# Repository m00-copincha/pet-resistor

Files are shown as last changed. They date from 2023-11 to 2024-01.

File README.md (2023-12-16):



# What is PET-Resistor?

PET-Resistor is a PET bottle 3D printing filament extruder, akin to [TheRecreator3D](http://recreator3d.com/), [Petamentor](https://petamentor2.com), and [PETalot](https://github.com/function3d/petalot), [FixStruder](https://www.fixstruder.eu/product/fixbot/). It combines the best features of these projects, emphasizing purpose and simplicity. Here are the key characteristics of PET-Resistor:

* **Self-replication:** the PET-Resistor filament extruder has self-replication capabilities like RepRap machines (https://reprap.org/wiki/RepRap), allowing it to contribute to its own production cycle.

* **Flat components:** we have adopted a pragmatic approach using flat components. These parts are designed using open source CAD software (such as Solvespace, OpenSCAD, Inkscape). These parts can be manufactured by laser, milling machine or 3D printing, which ensures their accessibility.

* **Inclusive design:** We intentionally minimize the manufacturing skills required so that more people can actively participate. We use the Openstructure modular system (https://www.openstructures.net/), which provides a common framework for adapting and creating components, encouraging collaboration and innovation.

Feel free to reach me out if you have any questions or want to get involved! 🌱🌟

# Contents

- [Getting Started](#getting-started)
- [Documentation](#documentation)
    - [Building the machine](#building-the-machine)
        - [Prerequisites](#prerequisites)
        - [Components](#components)
        - [The building flow](#the-building-flow)
    - [Using the machine](#using-the-machine) 
        - [Preparing the bottles](#preparing-the-bottles)
        - [Cutting the strips](#cutting-the-strips)
        - [Extruding](#extruding)
    - [3D printing with PET](#3d-printing-with-pet)

# Getting Started

For this project, you need the following programs:

* A 2D vector drawing software. You can use any one that allows you to export in SVG format. I am using:
    * SolveSpace, which allows you to make drawings with parametric constraints.
    * Inkscape, which allows you to draw vector graphics in a simple way.
* A 3D modeling software. You can use OpenSCAD, which allows you to import SVG files and apply an extrusion operation to give them thickness.

Another option is to create the drawing and the extrusion directly in SolveSpace, without using another program.

# Documentation

## Building the machine

### Prerequisites

### Components

- A bottle cutter built by:
    - 1 Threaded rod M8
    - 2 screws M8
    - 2 wing nuts M8
    - 1 cutter blade 9mm

- A power supply system, built by:

    - Power supply 110V 12V 10Amp (or more)
    - On/Off Switch 
    - Powercord 2m 

- A system to generate temperature in a controlled way, built by:

    - 3D Printer Heater Cartridge Wire 12V 40W
    - 3d printer heating block
    - REX-C100 Temperature Controller
    - K Type Thermocouple Temperature Probe Sensor
    - Relay 12V 10Amp
    - Computer Fan 12V 50mm x 50mm

- A system to rotate the reel in a controlled way, built with:

    - [DC 12V RPM Gear Motor](https://www.amazon.com/gp/aw/d/B07K9KPWX6) - High Torque Electric Micro Speed Reduction Geared Motor Centric Output Shaft 37mm Diameter Gearbox
    - Potentiometer module for the speed control for 12V 10 Amp

- Mechanical parts and structures made with fabricated or standardized parts.
    - screws 
    - nut
    - washer
    - 8 brace

To better understand the project we can see it from the origin of its components, so we have:

Purchased Components: these are the components that are purchased in the market, such as screws, bearings, cables, etc.

Recycled components: these are the components obtained from other objects or machines in disuse. These components are used to reduce the cost and environmental impact of the RepRap project.

Fabricated Components: these are components that are created with a RepRap machine or other tools, such as 3D printers, milling machines, etc. These were designed following the Openstructures grid.

### The building flow

1. Preparing the cutter module
    1.1 Place the screws on the cutter base and attach the wing nuts.
    1.2 Place threaded rod on the cutter base.
    1.3 Attach the cutter base to the cutter holder by screwing it together.

2. Preparing the hotend module
    2.1. Drill the hotend with a 1.7 mm drill bit.
    2.2. Drill the back of the heater with a 5mm drill bit.
    2.3. Attach the hotend to the hotend holder.
    2.4. Attach the ribbon guide to the hotend holder.
    2.5. Place the thermocoupler on the heatblock
    2.6. Place the resistor on the heatblock
    2.7. Insert cables through the orifice of the hotend holder

3. Preparing the power supply module
    3.1. Screw the power supply unit to the brackets

4. Prepare the ventilation module 
    4.1. Screw the fan to the inlet and outlet ventilation brackets.

5. Prepare the winder module
    5.1. Screw motor to motor holder.
    5.2. screw coupling to motor
    5.3. Screw the spooler to the coupling
    5.4. Screw the spooler
    
6. Preparing the tensioning rod module
    6.1. Assemble the pulley
    6.2. Place the pulley inside the shaft
    6.3. Fit the inner guide nuts
    6.4. Place wing nuts as outer guides

7. Prepare control modules
    7.1. Place the power switch on its holder 
    7.2. Place Pid control on its holder
    7.3. Place the speed control on its support.

8. Prepare relay module
    8.1. Assemble the relay bracket
    8.2. Solder wires to the relay
    8.3. Attach relay to bracket
    
9. Screw the brackets with the power supply to the bars. 

10. Assemble the frame
    10.1. Join the aluminum bars and the 3 longest covers.

11. Fit the two side covers. Insert the power cable through the hole in one of these side covers.
    11.1. Connect the power cable to the switch. 11.2. 
    11.2. Connect the switch to the power supply.
    11.3. Connect the PID control to the power supply.
    11.4. Connect the fan to the power supply. 
    11.5. Connect the speed control to the power supply
    11.6. Connect the motor to the speed control
    11.7. Connect thermocouple to PID controller
    11.8. Connect the resistor to the PID control

12. Assemble front face
    12.1. Place control modules in the front frame. 12.2.
    12.2. place relay module on the front frame
    12.3. Place ventilation modules.

13. Assemble rear face

14. Assemble bottom face

## Using the machine?

### Preparing the bottles

* Check if you have a PET bottle, look for the triangle symbol with the number 1 on the inside.

* Remove the labels and wash the bottles well both inside and outside.

* Inflate the bottles by applying air pressure. 

* Remove creases using a hot air gun.

* Remove glue using WD-40 and a srub sponge or a scrub brush.

* Finally wash the bottle with detergent to remove any remaining grease.

### Cutting the strips

* Cut the bottles into strips using a cutter. 

* It is important that the tape is homogeneous to obtain a good quality filament. 

* The width of the strips should be between 8 and 9 mm. A bottle of water is about 11 or 12 meters. The wider the bottle is cut the shorter the resulting strip will be.

### Extruding

* Start the machine and set the appropriate temperature.

* Cut the end of the strip into a fine tip shape that can pass through the nozzle of the heating block.

* Insert the tip of the strip into the nozzle and pull it until the length of the resulting extruded filament is long enough to connect it to the spooling cable.

* Connect the tip of the resulting extruded filament to the winder cable.

## 3D printing with PET

1. Printer Compatibility:

    * Many common 3D printers are not designed for printing with PET.

    * Make sure your printer can operate above 250 degrees Celsius.

    * Verify that the Teflon tube is able to withstand temperatures up to 260 degrees Celsius.

    * Filament traction is better when using a direct extruder, as the Bowden system has higher friction.
    
    * Comprobar el barrel. Cambiar el barrel de la impresora si este no tiene un diametro suficientemente grande para el filamento PET.

    * Opt for a 0.6 mm or 0.8 mm nozzle.Pue ser que este no tenga al diametro suficiente 

2. Firmware setup: 

    * The firmware of the printers usually comes with a maximum temperature of 275 degrees Celsius, but it has set a maximum safety limit of 15% below this temperature. This prevents the printer from reaching the optimal working temperatures, which are between 250 and 265 degrees. 
    
    * If it is necessary, modify this limit and set it to 0.

3. Temperature control:

    * PET can crystallize and cause jams. Jams can be caused by:
    
        * High temperature.
        * Too slow printing speed.
        * Too fast Fan speed.

    * Start with a minimum temperature of 250 degrees Celsius and adjust as needed. Increase in 5 degree increments if extrusion is uneven or if filament slips.

3. Bubble control:

    * Bubbles are related to moisture. This is not absorbed directly by the filament, but is trapped in the void during manufacturing.

    * Dry the filament properly to avoid bubbles. You can use a filament dryer.

3. Printing parameters:

* Layer fan speed: Between 0-15%

* Printing temperature: Between 250°C and 260°C

* Hot bed temperature: Between 70°C and 85°C

* Printing speed: 30 mm/s

* Flow: 130%

<br>

**Cura**

* Select an standard PETG filament profile

* Vertical walls: 3
* Horizontal walls: 4 (If son bases cuadradas 5 o 6) 

* Distancia de linea relleno 15.0mm

* Flow Balance:
    * for  5mm ribbon thicknes: 160%
    * for 10mm ribbon thickness: 

* Retraction distence: 5.5 mm
* Retraction speed: 30 mps

* tree support:
    * angle: 45

* borde:
    * adherencia impresion:
        * ancho de borde: 6

* activar modo experimental usar capas adaptativas

<br>

**PrusaSlicer**

* Select an standard PETG filament profile

In Filament Settings:

* Filament tab

    * Filament
        * Extrusion multiplier: 1.3

    * Temperature

        * Nozzle
            * First layer: 260°C
            * Other layers: 260°C

        * Bed 
            * First layer: 70°C
            * Other layers: 70°C
        
* Cooling tab
    * Enable 
        * Keep fan always on: Unchecked
        * Enable autocooling: Unchecked

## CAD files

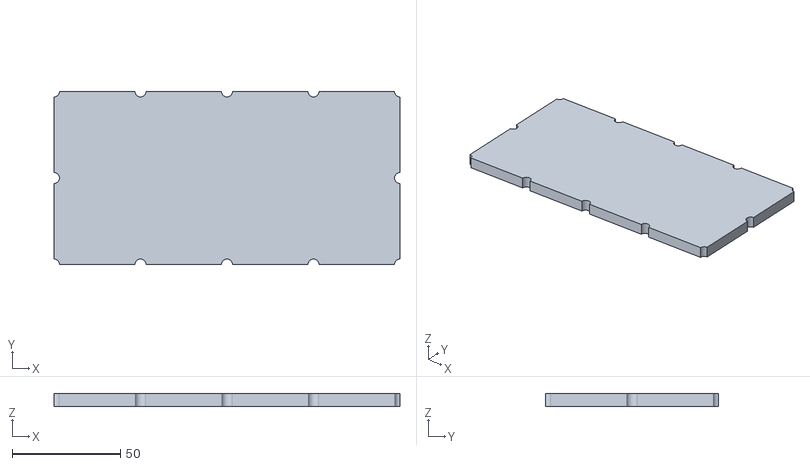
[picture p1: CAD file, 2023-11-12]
src/case/cover--back/cover--back--grid--logos.stl
160.0 x 80.0 x 6.00

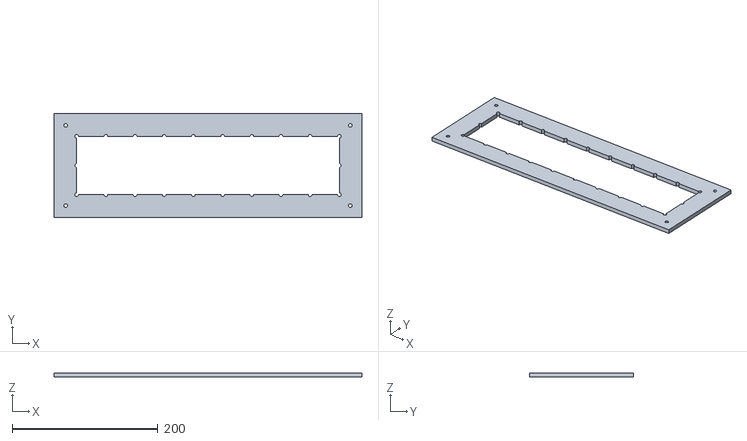
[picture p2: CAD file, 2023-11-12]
src/case/cover--bottom/cover--bottom--frame.stl
422.0 x 142.0 x 6.00

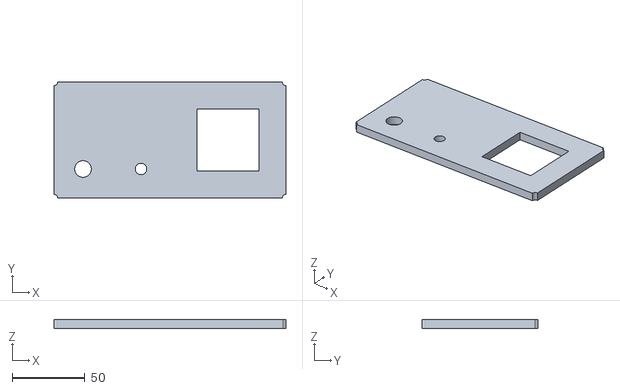
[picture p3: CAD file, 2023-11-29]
src/case/cover--front/cover--front--grid--control/cover--front--grid--control.stl
160.0 x 80.0 x 6.00

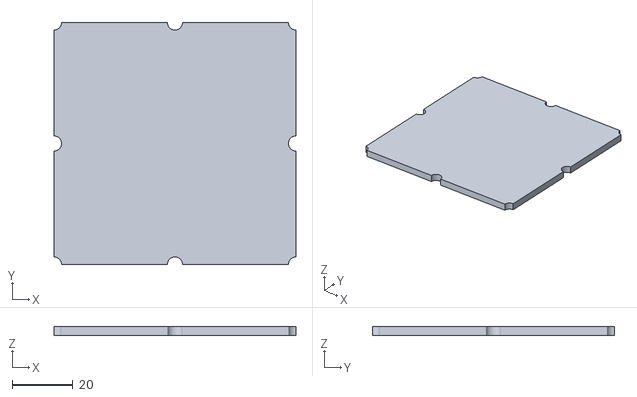
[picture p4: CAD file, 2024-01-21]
src/case/cover--grid--surface/cover--grid--surface--2x2.stl
80.0 x 80.0 x 3.00

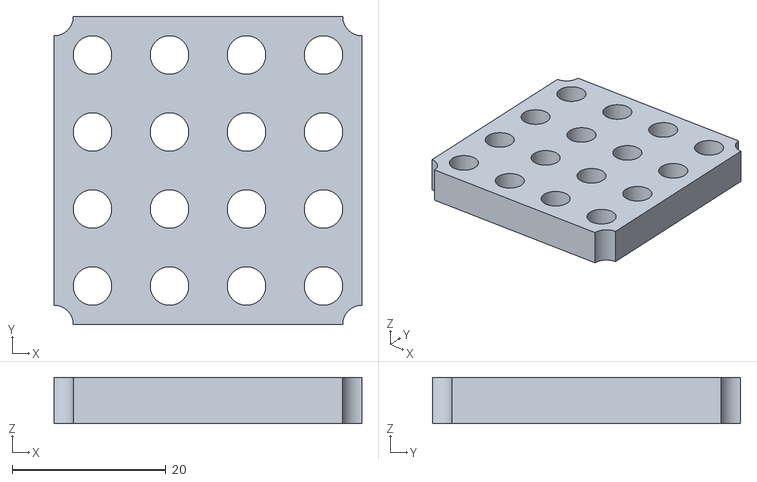
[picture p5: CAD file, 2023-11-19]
src/case/cover--grid--vent/cover--grid--vent--1x1.stl
40.0 x 40.0 x 6.00

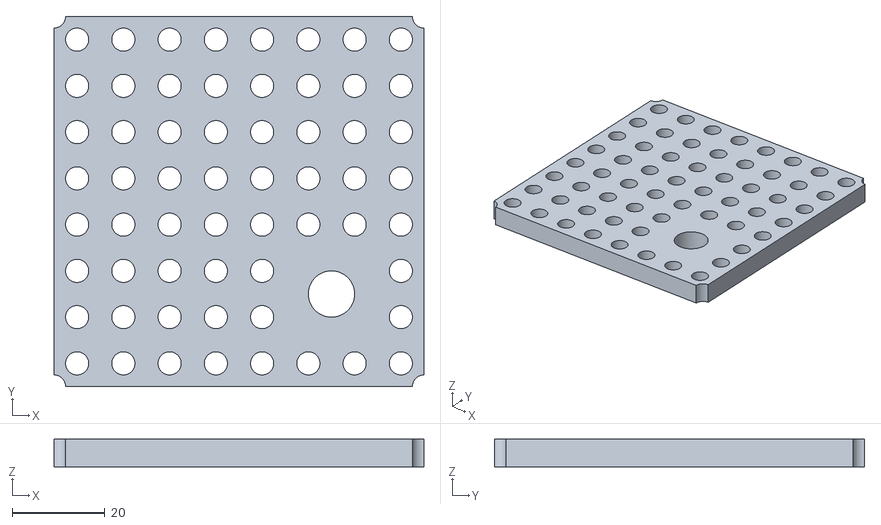
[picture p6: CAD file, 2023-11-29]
src/case/cover--left/cover--left--grid.stl
80.0 x 80.0 x 6.00

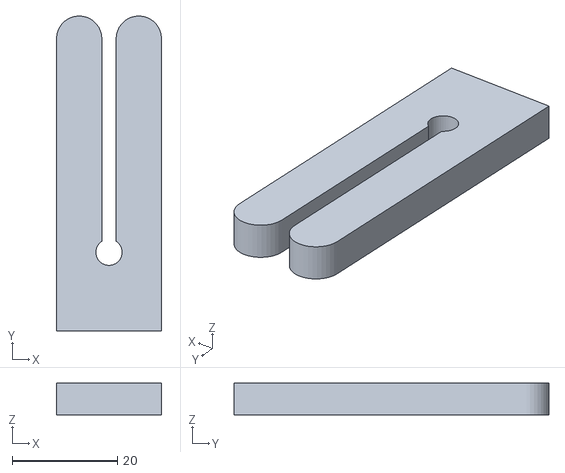
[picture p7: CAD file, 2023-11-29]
src/case/cover--top/cover--top--ribbon-holder.stl
20.0 x 60.0 x 6.00

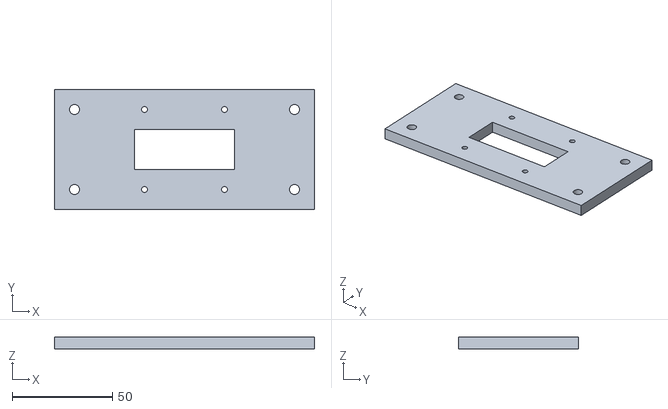
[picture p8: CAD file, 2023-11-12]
src/case/cover--top/fan-holder/case--fan-holder--ouput.stl
130.0 x 60.0 x 6.00

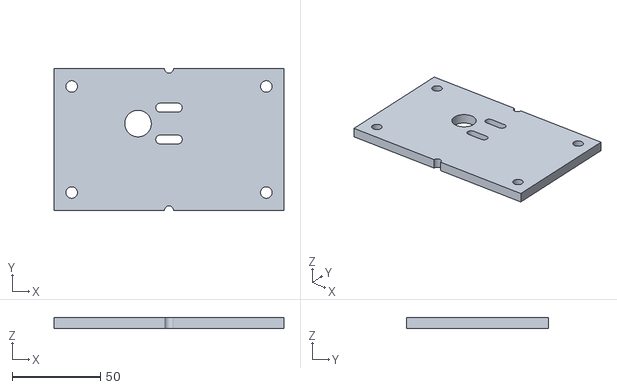
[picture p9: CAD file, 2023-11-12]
src/case/cover--top/hotend-holder/case--hotend-holder.stl
130.0 x 80.0 x 6.00

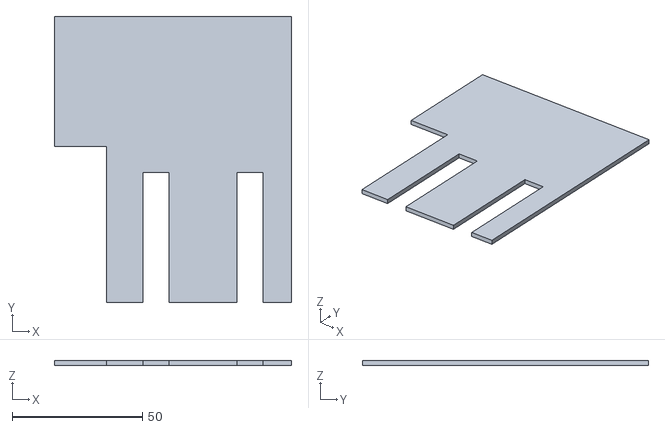
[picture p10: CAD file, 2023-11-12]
src/cutter--layout/cutter--layout.stl
91.0 x 110.0 x 2.00

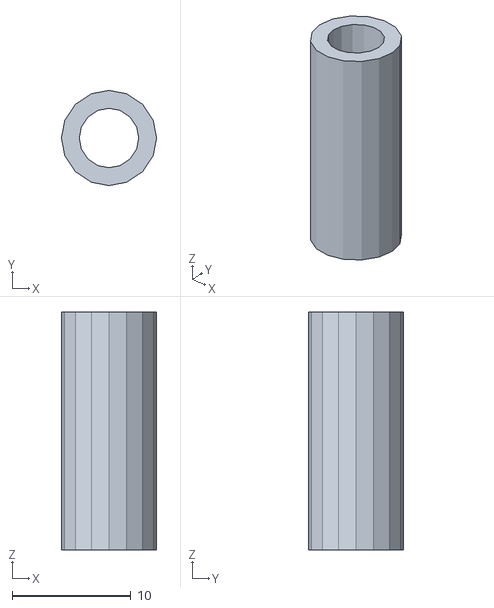
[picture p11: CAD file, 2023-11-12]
src/filament-hook--1.stl
8.00 x 8.00 x 20.0

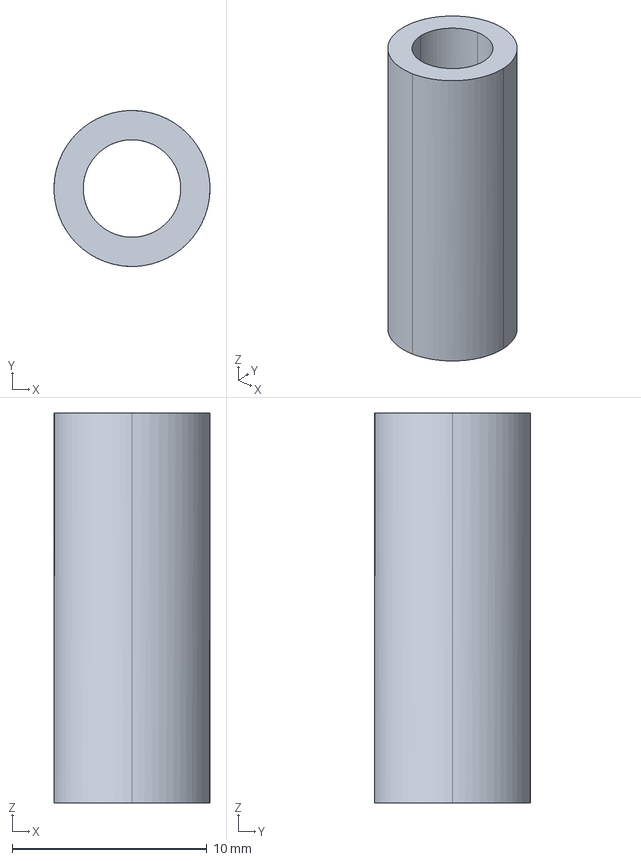
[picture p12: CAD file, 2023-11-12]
src/filament-hook/filament-hook--1.step
8.00 x 8.00 x 20.0 mm

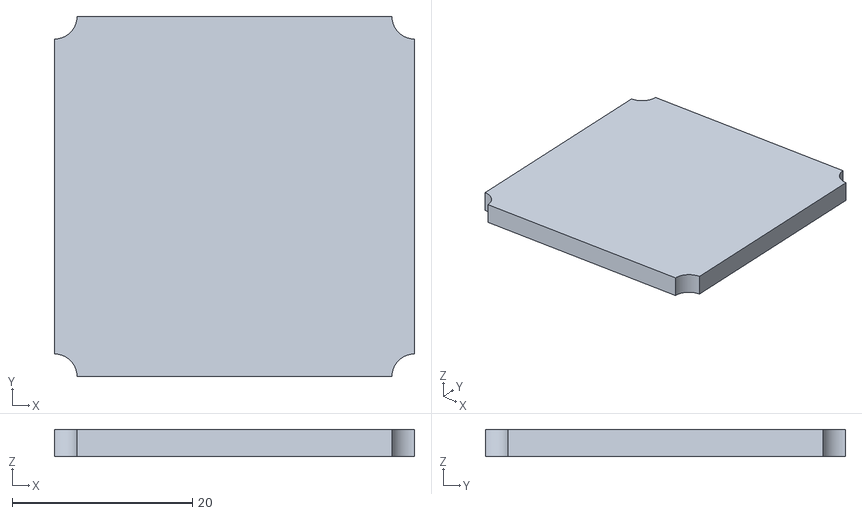
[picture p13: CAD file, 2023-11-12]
src/os-module/os-module--1x1.stl
40.0 x 40.0 x 3.00

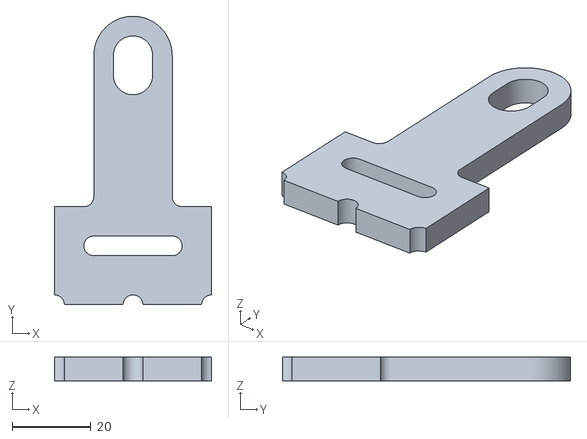
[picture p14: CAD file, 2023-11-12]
src/tensioning-rod/tensioning-rod--holder--m8.stl
40.0 x 73.5 x 6.00

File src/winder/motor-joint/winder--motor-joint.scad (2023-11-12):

//parameters

wall_thickness=3;
base_height=42;
coupling_thickness=8;
coupling_height=base_height-coupling_thickness;
svg_base="./winder--motor-joint--base.svg";
svg_hole_screw="./winder--motor-joint--hole--screw.svg";
svg_hole_coupling="./winder--motor-joint--hole--coupling.svg";


//operations

color("yellow")
translate([0,0,coupling_height-1]) 
linear_extrude(coupling_thickness+1)
import(svg_hole_coupling);

color("orange")
translate([0,0,coupling_height-wall_thickness])
linear_extrude(wall_thickness)
import(svg_hole_screw);

color("red")
linear_extrude(coupling_height)
import(svg_base);

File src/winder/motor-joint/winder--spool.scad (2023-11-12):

//modules

use <./winder--spool--front.scad>;
use <./winder--spool--base.scad>;


//parameters

wall_thickness=6;
spool_hight=42;


//operations

color("lightblue") 
translate ([0,0,spool_hight-wall_thickness])
winder_spool_front (h=wall_thickness);

color("blue") 
winder_spool_base (h_w=wall_thickness,h_s=spool_hight);

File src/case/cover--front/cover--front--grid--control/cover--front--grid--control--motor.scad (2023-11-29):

module cover_front_grid_control_motor (svg="./cover--front--grid--control--motor.svg",h=6) 
	{
	linear_extrude(h)
	import(svg);
	}

cover_front_grid_control_motor ();

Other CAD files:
src/case/cover--right/cover--right--grid.stl
src/winder/motor-joint/winder--motor-joint.stl
src/winder/spool/winder--spool--front.stl
src/case/cover--front/cover--front--grid--control/cover--front--grid--control--power.scad
src/case/cover--back/cover--back--frame.scad
src/case/cover--back/cover--back--grid--logos.scad
src/case/cover--back/cover--back--grid--vent.scad
src/case/cover--bottom/cover--bottom--frame.scad
src/case/cover--front/cover--front--frame.scad
src/case/cover--front/cover--front--grid--control/cover--front--grid--control--motor.stl
src/case/cover--front/cover--front--grid--control/cover--front--grid--control--pid.stl
src/case/cover--front/cover--front--grid--control/cover--front--grid--control--power.stl
src/case/cover--front/cover--front--grid--control/cover--front--grid--control--relay.scad
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

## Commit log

2023-11-12 adding parts and logo folders
    [bottle-cutter--body.stl, case--control--motor.scad, case--control--motor.stl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]
2023-11-12 moving parts in spool
    [bottle-cutter--body.stl, cutter--layout.scad, cutter--layout.stl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]
2023-11-14 adding text on readme.md
    [case--vent--1x1.scad]
2023-11-19 actualizando readme.md
    [case--vent--1x1.stl]
2023-11-29 updating readme
    [bottle-cutter--body.stl, case--control--motor.scad, case--control--motor.stl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]
2023-12-18 agregando video
    [bottle-cutter--body.stl, case--fan-holder--input.scad, case--fan-holder--input.stl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]
2023-12-18 actualizando src
    [bottle-cutter--body.stl, case--fan-holder--input.scad, case--fan-holder--input.stl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]
2024-01-21 update files
    [cover--front--grid--control--relay.scad, cover--grid--surface--1x1.scad, cover--grid--surface--1x1.stl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]
